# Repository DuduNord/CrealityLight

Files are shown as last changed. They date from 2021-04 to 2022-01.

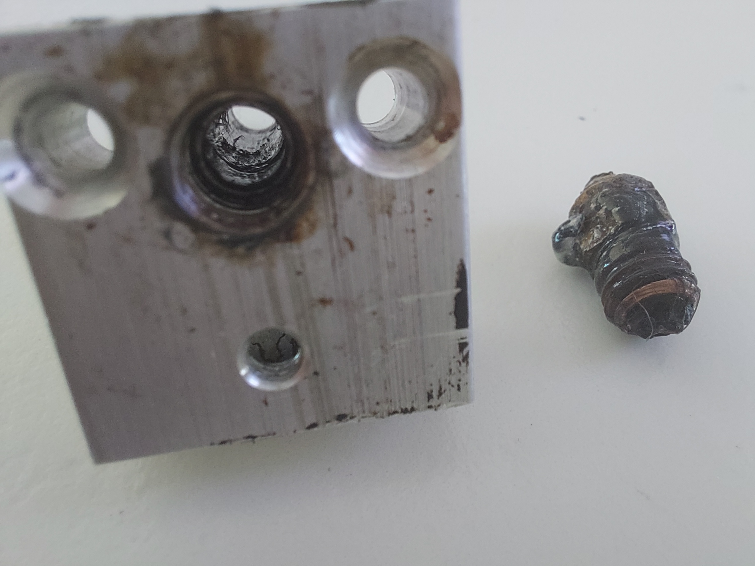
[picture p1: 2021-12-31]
For_Wiki/Issue1.jpg

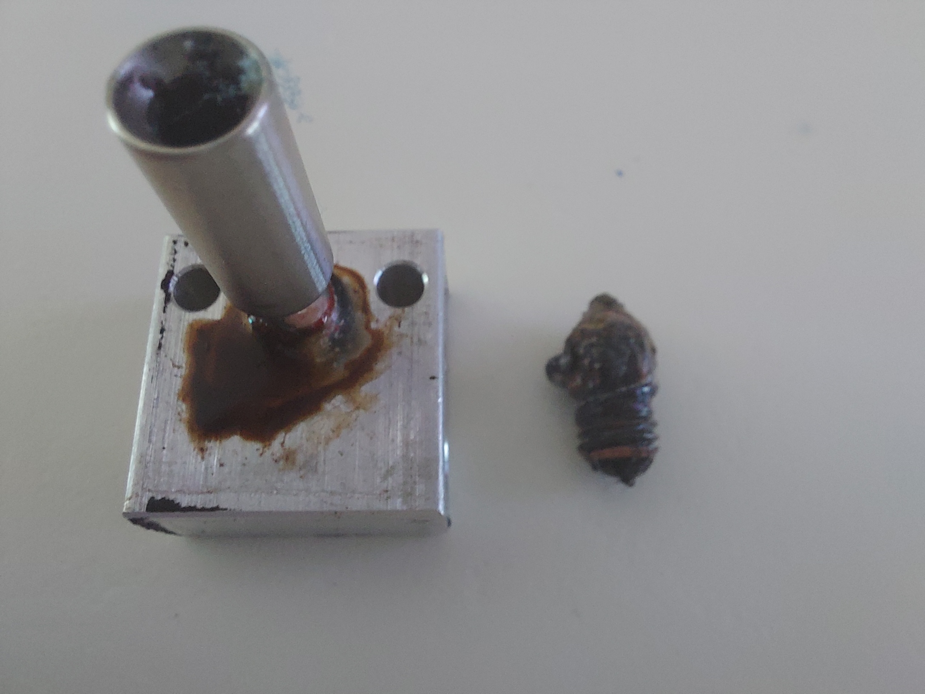
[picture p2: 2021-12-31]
For_Wiki/Issue2.jpg

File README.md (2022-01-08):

# CrealityLight V2 !!
## or how to connect a RPI/Ocroprint/Octoscreen and add some light 
### Read the wiki pages to get few more details.
This project does help how to connect a RPI to the octoscreen with a LED powerstage and a power relay.
This board does make the interface between the RPI and some MOS. 
But I have some doubt : 
- does the output of the relay goes to 0 when it is OFF ?
- how to turn on/off some LEDs manually without going to the octorpint interface, for a quick control ?
- how to turn off the RPI when the print is ended (the RPI can turn off the printer but may not turn it off) ?

I could have directly connected the RPI to the MOS, but I have decided to add an ATTINY1614 to add some flexibility.
I have added a puchbutton for some local interraction :
1. the pushbutton can turn on/off 3 different LED sting
1. it can also turn on/off a local LED (3V3) close to the extruder, to see the filament hole when we change it (this LED is not driven by the pi, only by the user because it is used to bring some light when I am changing the filament (I am not ont the onctoprint web interface)) 
1. it can force the RPI to be turned OFF locally :
   1. immediately (turn off the printer also)
   1. after a cooldown delay : the RPI is turned off immedately and the printer after some time (delay fixed in the ATTINY firmware)
   1. after a print, when the RPI does turn off the printer because of the idle time.
I also connect an emergency push button (direct connection) and plan to use a SmartFilamentSensor

## ATTINY connection

The Attiny does have to communicate with the PI. it has then to work under a 3.3V. The PRI does then provide a 3.3V to the ATTINY
The RPI is powered from the main printer AC/DC through a simple USB DC/DC. I have used a mEZS91202A from MPS (MonolithicPowerSystem) becaue of its simple connection. It can also deliver 2.5A : 
- https://www.monolithicpower.com/en/mezs91202a.html
- you can also consider a mEZD71202A-G for a 2A rail from 24V input (maybe it can also handle 3A)

The scheamtic and layout is in this project
The connection does use the end of the GPIO connector, to be able to use a touchscreen display for octodash/octoscreen : 
RPI GPIO | RPI BCM | ATTINY pin | ATTINY port | Signal description
-------- | ------- | ---------- | ----------- | ------------------ 
31 |  6|  4|  PA6| LED1IN
32 |  12|  3|  PA5| LED2IN
33 |  13|  2|  PA4| RelayIN : output of the PI to turn ON/OFF the relay
34 |  GND|  14|  GND| 
36 |  16|  5|  PA7| RPIReset : input for the PI, to be turned off
37 |  26|  na|  na| Emergency stop : push button to turn off a print if something goes wrong
38 |  20|  7|  PB2| OctoprintReady: signal from octoprint saying that it is alive
40 |  21|  na|  na| SmartSensor input : logic signal from a filament sensor

On the ATTINY board connector this mean :
ATTINY pin | ATTINY port | Arduino port | Signal description
---------- | ----------- | ------------ | ------------------
1 | 3.3V |  | power from a LDO on the board
2 | PA4 | 0 | RelayIN : signal from the PI
3 | PA5 | 1 | LED2IN : signal from the PI
4 | PA6 | 2 | LED1IN : signal from the PI
5 | PA7 | 3 | PI Reset : signal from the arduino to the PI to turn it off
6 | PB3 | 4 | PushButton : loacl button to select the action : turn ON/OFF the led or select which PI turn-off senario
7 | PB2 | 5 | OctoPrint Ready : signal from the PI saying that octoprint is ready (set to 1 when active)
8 | PB1 | 6 | LEDOUT : simple 3.3V LED, used for the Extruder
9 | PB0 | 7 | LEDPOWEROUT1 : MOS to 24V to drive one LED string
10 | UPDI | na | 
11 | PA1 | 8 | LEDPOWEROUT2 : MOS to 24V to drive one LED string
12 | PA2 | 9 | LEDPOWEROUT3 : MOS to 24V to drive one LED string
13 | PA3 | 10 | RELAYOUT : MOS to 24V to drive the printer relay
14 | GND |  | 

## Octoprint pluggins and config (see also the wiki)
quick note : the pluggin that turn off the RPI on a GPIO state has to be very carefully installed. I would recommend to disable the pin each time you disable it. otherwise, when you enable the pluggin in the octoprint "Pluggin Manager" it will immediately set the pin and activate it. And then your PI may turn off immediately becasue the pin is not driven

quick note : the pluggins can use GPIO or BCM numbering. Some give the choice like PSU Control. I would think that there is a mix when each pluggin does try to name the pins with different method. For the moment, the BCM method seems to be more functional.  

### Autoscroll (0.0.3)
### Bed Visualizer (1.0.0)
### BetterHeaterTimeout (1.3.0)
### Creality-2x-temperature-reporting-fix (0.0.4)
### DisplayLayerProgress Plugin (1.25.3)
### Emergency Stop Simplified (0.1.1) 

By default the pluggin does apply a pull-up or pull-down and check if the switch is open. If the button is set to GND, the pluggin does set a pull-up and will stop ONLY if the voltage is pulled-up by the internal pull-up resistor. By checking with an multimeter, I was no able to see a 3.3V on the pin when the switch is activated (open). I had a look then on the log (cd .octoprint/logs and then go really down to nano octoprint.log) and see the message : 
```
File "/home/pi/oprint/lib/python3.7/site-packages/octoprint_emergencystopsimplified/__init__.py", line 59, in _setup_button
    GPIO.setmode(GPIO.BCM)
ValueError: A different mode has already been set!
```
I tried then to change the mode from BCM to BOARD. I change the pin number to 37 (value in GPIO mode). A complete restart and I have been able to see that my pull-up was then present (I can see the voltage going up to 3,3V when the button is activated). During the print the printer goes immediately offline.

Note : Alexiri pluggin has the choice to turn off the printer or make a pause : https://github.com/alexiri/Emergency_stop_simplified/blob/master/octoprint_emergencystopsimplified/

Note : crysxd pluggin has the choice to select if the action is performed when the switch is going to open or closed state.
> would need to add an option to select BCM OR GPIO mode. And add a test mode like for the SmartFilament Sensor that has a specific "motion" test

My configuration: pin = 32 (GPIO pinout because I change from BCm to GPIO in the __init__.py) and button connected to ground.

### Exclude Region (0.3.0)
### Floating Navbar (0.3.4)
### Fullscreen Plugin (0.0.6)
### GPIO Shutdown (1.0.3)
- this pluggin would have worked perfectly but it seems to mix at start-up the BCM and GPIO pins. to get it funcional, I have to select in the setup the GPIO number that I want (and not the BCM one) and save. Then the LED is turned ON immediately. Consider to use instead a simple script/service that is available on the web and out of octoprint. I wil otherwise change the Jinja config file to link the BCM pin to the GPIO.
- the pluggin location is in "~/oprint/lib/python2.7/site-packages/octoprint_GPIOShutdown"
- to get it functional, I have changed manually the JINJA2 file to allow the selection of pins up to 40. By doing this, I can select a high pin number.
- My setup : shutdown on pin GPIO36 / PIN LED : GPIO 38 with default debounce time.
- To get this, i have to change the jinja file the selection menu for both the led and the shutdown pin:
```
cd ~/oprint/lib/python2.7/site-packages/octoprint_GPIOShutdown/templates/
nano GPIOShutdown_settings.jinja2
                                <option value="-1">Disabled</option>
                                <option value="2">BCM 2</option>
                                <option value="3">BCM 3</option>
                                <option value="4">BCM 4</option>
                                <option value="5">BCM 5</option>
                                <option value="6">BCM 6</option>
                                <option value="7">BCM 7</option>
                                <option value="8">BCM 8</option>
                                <option value="9">BCM 9</option>
                                <option value="10">BCM 10</option>
                                <option value="11">BCM 11</option>
                                <option value="12">BCM 12</option>
                                <option value="13">BCM 13</option>
                                <option value="14">BCM 14</option>
                                <option value="15">BCM 15</option>
                                <option value="16">BCM 16</option>
                                <option value="17">BCM 17</option>
                                <option value="18">BCM 18</option>
                                <option value="19">BCM 19</option>
                                <option value="20">BCM 20</option>
                                <option value="21">BCM 21</option>
                                <option value="22">BCM 22</option>
                                <option value="23">BCM 23</option>
                                <option value="24">BCM 24</option>
                                <option value="25">BCM 25</option>
                                <option value="26">BCM 26</option>
                                <option value="27">BCM 27</option>
                                <option value="3">GPIO 3</option>
                                <option value="5">GPIO 5</option>
                                <option value="7">GPIO 7</option>
                                <option value="8">GPIO 8</option>
                                <option value="10">GPIO 10</option>
                                <option value="11">GPIO 11</option>
                                <option value="12">GPIO 12</option>
                                <option value="13">GPIO 13</option>
                                <option value="15">GPIO 15</option>
                                <option value="16">GPIO 16</option>
                                <option value="18">GPIO 18</option>
                                <option value="19">GPIO 19</option>
                                <option value="21">GPIO 21</option>
                                <option value="22">GPIO 22</option>
                                <option value="23">GPIO 23</option>
                                <option value="24">GPIO 24</option>
                                <option value="26">GPIO 26</option>
                                <option value="29">GPIO 29</option>
                                <option value="31">GPIO 31</option>
                                <option value="32">GPIO 32</option>
                                <option value="33">GPIO 33</option>
                                <option value="35">GPIO 35</option>
                                <option value="36">GPIO 36</option>
                                <option value="37">GPIO 37</option>
                                <option value="38">GPIO 38</option>
                                <option value="40">GPIO 40</option>
```
Backup : a local service routine:  
Let's try with this config (https://www.instructables.com/Simple-Raspberry-Pi-Shutdown-Button/) to get a shutdown on level 1 because the ATTINY when OFF (not powered-up) will pull the pin low :
gpio_pin_number=21
GPIO.setmode(GPIO.BCM)
GPIO.setup(gpio_pin_number, GPIO.IN, pull_up_down=GPIO.PUD_DOWN)
try:
    GPIO.wait_for_edge(gpio_pin_number, GPIO.RISING)
    os.system("sudo shutdown -h now")
except:
    pass
GPIO.cleanup()

### LED Strip Control (0.3.7) (not installed)
### LightsOut (0.1.2)
### Multi Colors (1.0.17) 
### OctoLight (0.1.1)
> Configuration : Light pin = 38
### PSU Control (0.1.11)
to be changed, checked : For some reason, the pluggin does not work if the pin mode is GPIO. But it does work well when the BCM mode is selected. you need to change again th python to select the "BOARD" mode instead of "BCM"
> Configuration : GPIO mode : Board > GPIO pin > 37 // internal sensing (5s)
### Simple Emergency Stop (1.0.4) 
### Smart Filament Sensor (1.1.5.3)
Board mode / pin 40 with the button "enable sensor" checked > command M600 (to be tested), detection mode : distance set at 15mm (default value)
and then tested with the small test button
### Tab Order (0.5.12) 
### not acivated - Octoprint-Display-ETA (1.1.3) 
### WebcamTab (0.2.0)

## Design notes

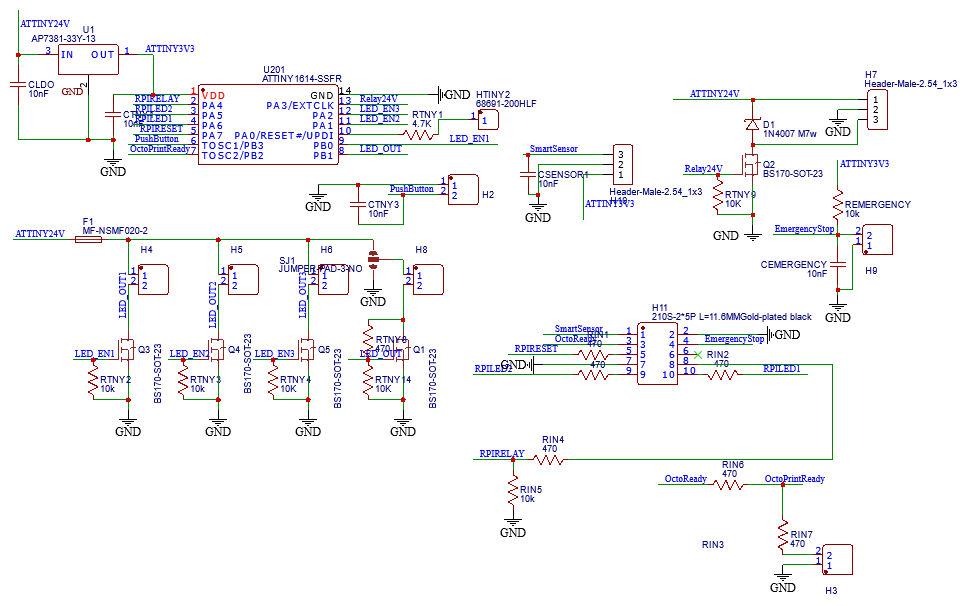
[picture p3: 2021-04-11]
Schematic_CrealityLight_2021-04-11.png

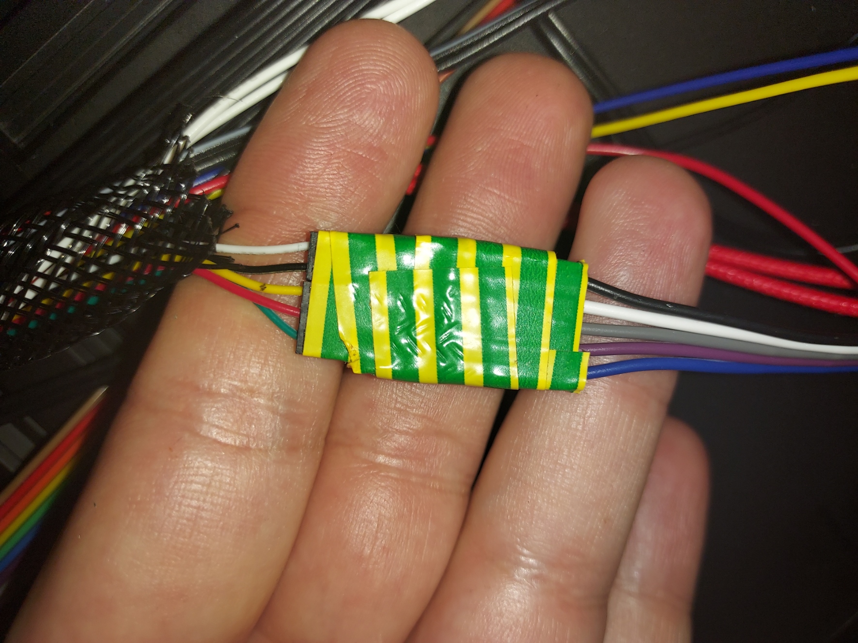
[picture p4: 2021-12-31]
For_Wiki/BLTOUCH_picture2.jpg

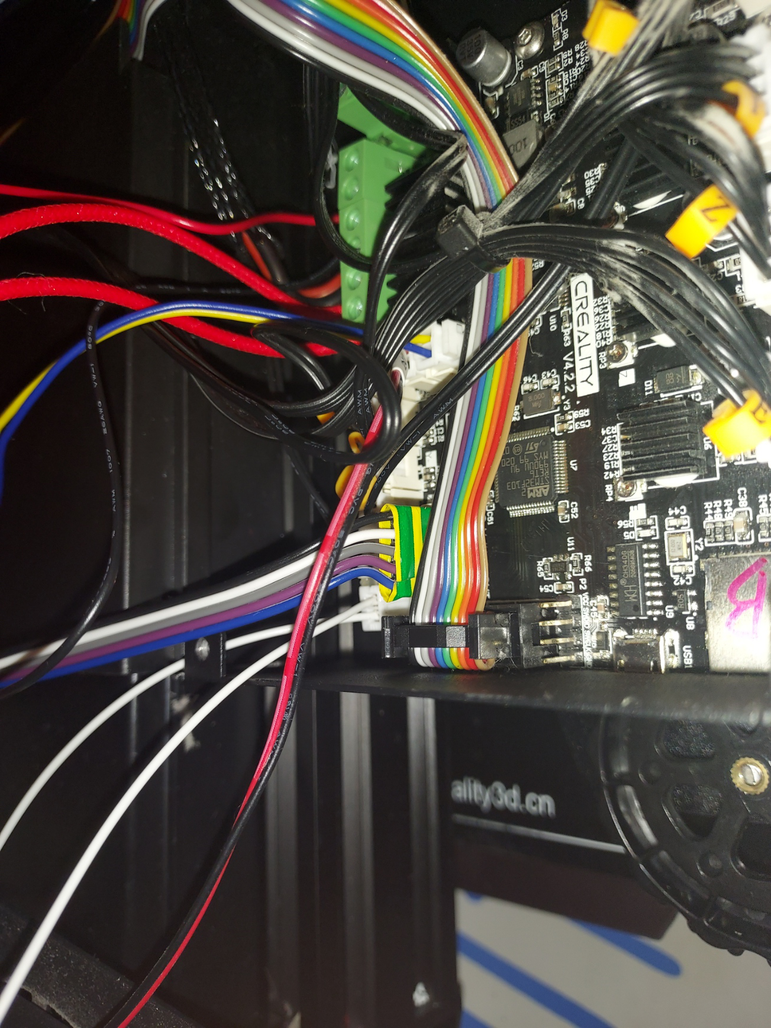
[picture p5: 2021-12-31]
For_Wiki/BLTOUCH_picture1.jpg

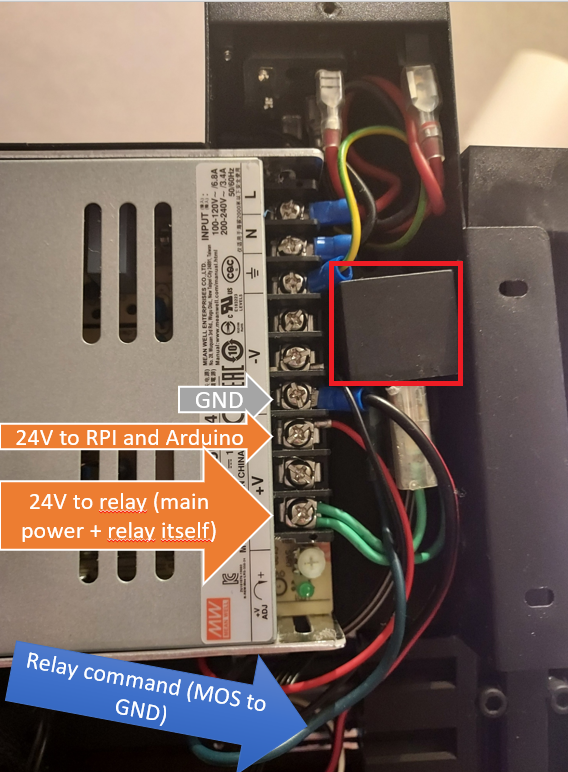
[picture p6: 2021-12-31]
For_Wiki/RelayCreality.png

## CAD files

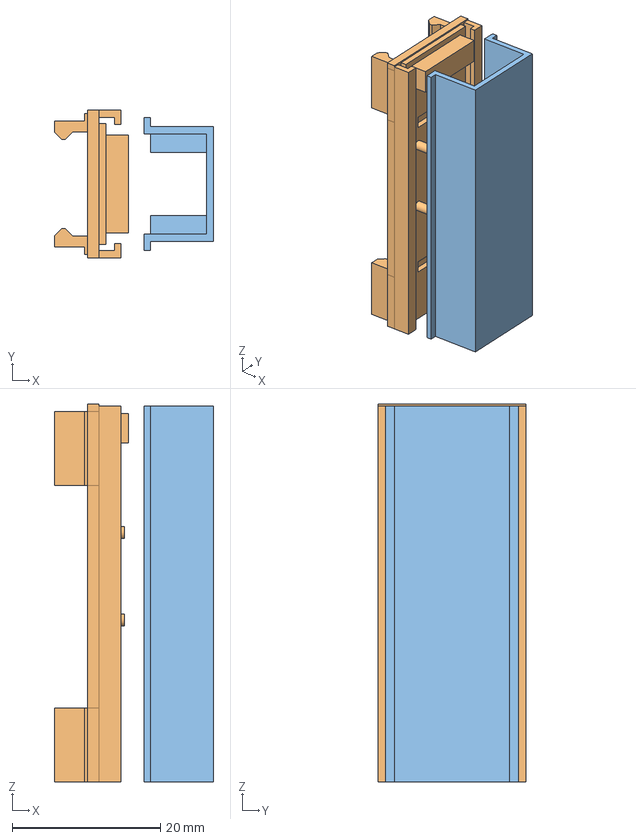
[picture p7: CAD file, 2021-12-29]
RailEnder3USB-V2.FCStd
21.5 x 20.0 x 51.0 mm
SupportUsbBase
SupportUsbAClipper
Capot

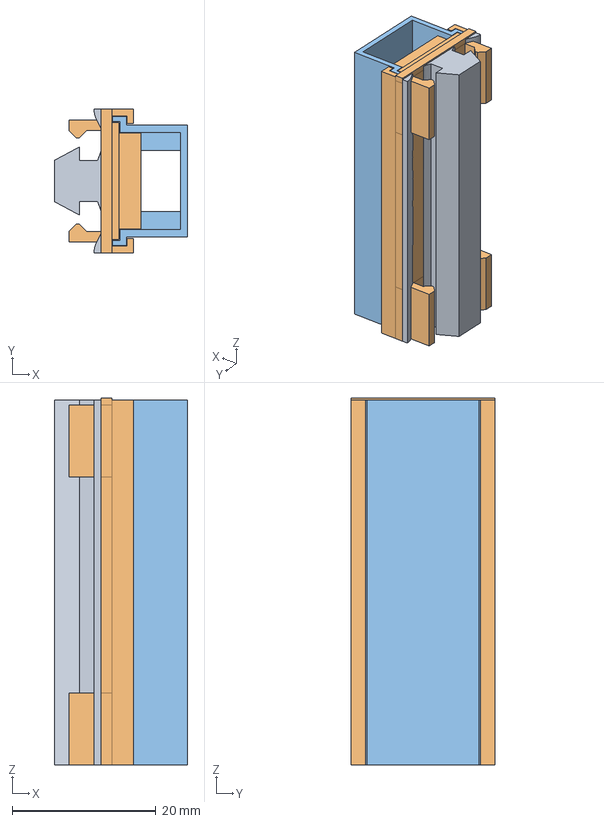
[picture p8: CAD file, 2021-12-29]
RailEnder3USB.FCStd
18.5 x 20.0 x 51.0 mm
RailAGlisser
SupportUsbAClipper
Capot

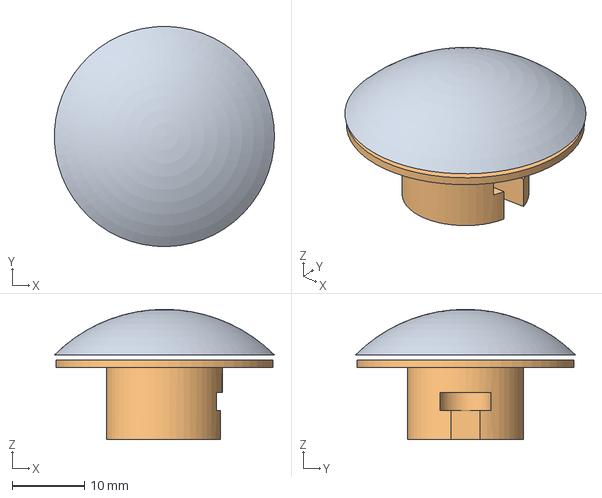
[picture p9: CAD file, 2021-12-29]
EmmergencyChampi.FCStd
30.4 x 30.4 x 18.0 mm
Champignon

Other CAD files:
RailEnder3USB-V2.stl

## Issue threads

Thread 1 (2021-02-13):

Printer turned on at startup

DuduNord, 2021-02-13:

DuduNord, 2021-02-13:
Am implementing a sensing methid that wait for the RPI to turn off the relay before going into the main program

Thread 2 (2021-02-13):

When the RPI is not present or not functional/booting, no printer available

DuduNord, 2021-02-13:
If the RPI can't work, for any reason, the printer can't be turned on. this could be manage by pull-up/down resistor if the PI is not present. But to be sure, and to avoid any effect on ISSUE1 (does wait a modification of relay command to turn on), will implement a sensing method with the button : if the button is activated at power on, the relay is always on immediately> the RPI will not be able to turn on/off the printer. anyway  the LEDs will stay active from the RPI or the push button

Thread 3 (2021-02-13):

At power down, printer restart

DuduNord, 2021-02-13:
When the end user does urn off the RPI through the ATTINY, (4 click/5 click or long press), the ATTINY does know that the RPI is turned off (becasue it does it itself). Then the Relay and lights are also turned off. but when the end-user turn off the printer and the RPI remotely (push-button not activated), the ATTINY will turn on again the printer and the light again (same root cause than issue 1). Unfortunately there is no way for the  ATTINY to know that Octoprint is used.
To fix this, we will use PSUControl pluggin to indicate (by a signal, was planned to be a LED) that octoprint is up and running. ATTINY will have only one LED signal and we will use the second LED signal (not used in my case for the moment) to get this signal and "sense" octoprint activity.
At boot it will not trust the pin but will get its variable "RPI eteint" (=RPI turned off) to "true" to know that it is turned off.

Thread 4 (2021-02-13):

When use OctoRemote, I can't start the printer because PowerOn button from PSU Control pluggin not present

DuduNord, 2021-02-13:
If I want to launch a print from the smartphone, I can't turn on the printer because the app does not show the on/off button from the pluggin. I need then to go through the internet interface to turn on the printer.

DuduNord, 2021-02-13:
To overcome this, will implement a funciton in the boot : if the button is activated when the power is applied, the printer will be turned on, whatever the PI status (if present or not, if booting or functional). Later if the RPI is connected, it will be possible to "recover" the ON/OFF function from the PI, by turning on the button on the web page.

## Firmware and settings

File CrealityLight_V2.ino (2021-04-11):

/* V3: utilisation d'une entrée GPIOSHUTDOWN

 * FONCTIONNEMENT LED : 
 * si le pi n'a pas activé la lumière LED2  alors l'utilisateur peut allumer éteindre avec respectivement un appui simple et un double appui
 * si le pi n'a pas activé la lumière LED1, un appui long allume LED1 et le relachement l'éteint
 * si l'utilisateur appui 3 fois, éteint/allume la LED de l'extrudeur * Fonctionnement Relais/extinction
 * la sortie LED3 n'est pas utilisé
 * FONCTIONNEMENT EXTINCTION
 * si l'utilisateur appui 4 fois, l'Arduino éteindra le PI lorsque le PI éteindra l'imprimante (mode suicide). Autre 4 click = annule l'extinction
 *   si l'utilisateur a validé l'extinction du PI par le bouton, alors éteindra le PI en activant la pin "RPIReset" après un certain délais (idéalement passage de 0 à 1 pui de 1 à 0)
 *   Mais l'utilisateur peu désactiver cette extinction avec la même séquence (4 appui)
 * si l'utilisateur appui 5 fois, l'Arduino éteind le PI immédiatement et éteindra l'imprimante après un délais pour la laisser refroidir. Pas d'annulation possible
 * Si l'utilisateur fait un appui long sur le bouton, alors l'Arduino éteint tout immédiatement (imprimante et PI)
 * NOTE : a la sélection de 4 ou 5 appuis, la LED de l'extruder clignotera du meme nombre de click, pour valider la prise en compte
 * A FAIRE : 
 *    Alimentation de l'imprimante au démarrage si on appuie sur le bouton au démarage
 */

/*        PINOUT
 *        ------
 *          VDD  |      |GND
 *RelayIN/0/PA4  |      |PA3/10 /RelayOut
 *LED2IN /1/PA5  |      |PA2/9  /LedPowerOut3
 *LED1IN /2/PA6  |      |PA1/8  /LedPowerOut2
 *RPIRst /3/PA7  |      |PA0/11 /ISP
 *PushBut/4/PB3  |      |PB0/7  /LedPowerOut1
 *OctoRdy/5/PB2  |      |PB1/6  /LedOut
 *        ------*/

/* SOIC  Pin   Arduino  ADC0  ADC1  DAC0  USART0  SPI0  TWI0  TCA0  TCBn    TCD0  CCL   
 * 10    PA0   11       AIN0  -     -     -       -     -     -     -       -     LUT0-IN0  > ISP
 * 11    PA1   8        AIN1  -     -     TXDbis  MOSI  SDA   -     -       -     LUT0-IN1  > LedPowerOut2
 * 12    PA2   9        AIN2  -     -     RXDbis  MISO  SCL   -     -       -     LUT0-IN2  > LedPowerOut3
 * 13    PA3   10       AIN3  -     -     XCKbis  SCK   -     WO3   TCB1 WO -     -         > RelayOut
 * 14    GND            -     -     -     -       -     -     -     -       -     -         >
 * 1     VDD            -     -     -     -       -     -     -     -       -     -         >
 * 2     PA4   0        AIN4  AIN0  -     XDIRbis SS          WO4           WOA   LUT0-OUT  > RelayIN > RPI PIN 33
 * 3     PA5   1        AIN5  AIN1  -     -       -     -     WO5   TCB0 WO WOB             > LED2IN > RPI PIN 32
 * 4     PA6   2        AIN6  AIN2  OUT                                                     > LED1IN > RPI PIN 31
 * 5     PA7   3        AIN7  AIN3  -     -       -     -     -     -       -     LUT1-OUT  > RPIReset
 * 6     PB3   4        -     -     -     RXD     -     -     WO0bis                        > PshBut
 * 7     PB2   5        -     -     -     TXD     -     -     WO2                           > OctoReady > > RPI PIN 38 (BCM GPIO20)
 * 8     PB1   6        AIN10 -     -     XCK     -     SDA   WO1                           > LedOut
 * 9     PB0   7        AIN11 -     -     XDIR    -     SCL   WO0                           > LedPowerOut1
 */

#include "EButton.h"
#define DEBUGMODE         // le laisser car le reste est pas testé (prise en main )

/* ---------------------------------------------------------- */
/* ------------------  HARDWARE  ---------------------------- */
/* ---------------------------------------------------------- */
/* Ajouter ATTINY1614 dans Arduino : 
 *  https://create.arduino.cc/projecthub/john-bradnam/using-the-new-attiny-processors-with-arduino-ide-612185
 * Arduino : MegaTinyCore>>ATTINY1614....
 * Bootloader : jtag2updi (megaTinyCore) à base d'un Arduino Nano Old bootloader
 * Info > BOD Volt:2,6V // Clock 1MHz // Mili by default // UART close to 3V
 * please reade this great tutorial to know what you can do with ATTINY MegaTinyCore : https://github.com/SpenceKonde/megaTinyCore 
*/
/* ---------------------------------------------------------- *
 * -------------------  PINOUT  ----------------------------- *
 * ---------------------------------------------------------- */
#define LedPowerOut1        7  //PB0 > SORTIE transistor LED
#define LedPowerOut2        8  //PA1 > SORTIE transistor LED
#define LedPowerOut3        9  //PA2 > SORTIE transistor LED
#define LedOut              6  //PB1 > SORTIE simple LED pour extrudeur
#define RelayOut            10 //PA3 > SORTIE relais 24V/16A
#define RPIReset            3  //PA7 > SORTIE : sortie à la 0 pour éteinde le pi
#define PshBut              4  //PB3 > ENTREE SEULE bonton poussoir en pull-up de commande pour interface homme Arduino
#define LED1IN              2  //PA6 > ENTREE VENANT DU PI
#define LED2IN              1  //PA5 > ENTREE VENANT DU PI
#define RelayIN             0  //PA4 > ENTREE VENANT DU PI
#define GPIOSHUTDOWNIN      5  //PB2 > ENTREE VENANT DU PI INDIQUANT SI OCTOPRINT EST PRET OU PAS

EButton button(PshBut);     //bouton pressé quand à la masse

/* ---------------------------------------------------------- */
/* -----------------  CONSTANTES  --------------------------- */
/* ---------------------------------------------------------- */
// pour séquence d'initialisation
#define DelaisStartup                         60000    // délais avant que l'ATTINY commence sa boucle principale et allume le relais et les lumières. nécessaire car pendant le boot, le PI allume le relais temporairement

// variables 
#define DureePression                         984    // en milli secondes
#define DureePressionLongue                   3000   // en milli secondes
#define DelaisExtinctionPiParPi               1000   // délais (ms) entre le moment ou l'imprimante est éteinte par le PI et le moment ou le PI est éteint par l'Arduino
#define DelaisExtinctionPiRefroidissement    120000  // délais (ms) entre le moment ou l'Arduino détecte une extinction et le moment ou il éteint l'imprimante (délais nécessaire pour refroidir le bed et l'extrudeur)
#define DelaisExtinctionPiImmediat            1000   // délais (ms) entre le moment ou l'imprimante est éteinte et le moment ou le PI est éteint (extinction immédiate)
#define DelaisReboot                          60000   // délais (ms) entre le moment ou l'imprimante est éteinte et le moment ou le PI est éteint (extinction immédiate)
#define DeglitchRelaisIn                      400    // délais (ms) pendant lequel l'entrée venant du pi doit rester à 0 avant l'extinction réelle du relais de l'imprimante

#define LED1PWM                      255          // valeur de PWM entre 0 et 255
#define LED2PWM                      255
#define LED3PWM                      255          // pas implémenté pour le moment
#define LED4PWM                      255          // sortie extrudeur

#define PIRESETE                      1           // Etat a applique pour éteindre le PI
#define PIFONCTIONNE                  0           // Etat a applique pour laisser le PI fonctionner

// constantes pour mieux lire l'état de GPIOSHUTDOWNSequenceVerif
#define STARTUP                       0
#define WAITTOBOOT                    1
#define BOOTED                        2
#define POTENTIALREBOOTED             3
#define TURNEDOFF                     4

/* pour changer la vitesse de clock, pas utilisé
#define MCLK_PRESC_2    0x00
#define MCLK_PRESC_4    0x01
#define MCLK_PRESC_8    0x02
#define MCLK_PRESC_16   0x03
#define MCLK_PRESC_32   0x04
#define MCLK_PRESC_64   0x05
#define MCLK_PRESC_6    0x08h
#define MCLK_PRESC_10   0x09
#define MCLK_PRESC_12   0x0A
#define MCLK_PRESC_24   0x0B
#define MCLK_PRESC_48   0x0C */

/* ---------------------------------------------------------- */
/* -----------------  VARIABLES  ---------------------------- */
/* ---------------------------------------------------------- */
bool ExtinctionPiParPi = false;      // TRUE, si l'utilisateur a demandé à éteindre le PI en même temps que l'imprimante, 
bool ExtinctionPiRefroidissement = false;      // TRUE, si l'utilisateur a demandé à éteindre le PI après un délais de refroidissement, 
bool ExtinctionPiImmediat = false;      // TRUE, si l'utilisateur a demandé à éteindre le PI immédiatement 
bool EntreePiRelais = false;            //variables pour le deglich de l'entrée relais venant du PI
bool EntreePiRelaisPrev = false;
bool EtatRelais = false;                // donne l'état du relais

uint8_t EtatRelaisBoot = 0;                // donne l'état du relais au boot du PI
uint8_t EtatGPIOSHUTDOWNIn = 0;            // donne l'état de la pin de status "GPIOShutdown" au boot, pour voir si elle bagotte ou reste à 0
uint8_t GPIOSHUTDOWNSequenceVerif = STARTUP;     // donne l'état du relais au boot du PI
bool EtatBoutonBoot = false;                // donne l'état du bouton poussoir au boot
uint8_t EtatBoutonBootPrev = 0;             // donne l'état du relais au boot du PI, UINT pour le comparer directement à la lecture de l'entrée qui renvoie un entier 0 ou 1 (pourrait fonctionner avec un bool mais bon....)
bool BoutonNotActivated = true;             // indique si le bouton a été activé ou non pendant le boot
bool BootTimerEnded = false;                // indique si le timer de boot s'est terminé sans changement d'état de pin du PI

bool EntreePiLED1 = false;            //variables pour le deglich de l'entrée LED1 venant du PI
bool EntreePiLED1Prev = false;
bool EntreePiLED2 = false;            //variables pour le deglich de l'entrée LED2 venant du PI
bool EntreePiLED2Prev = false;

bool PiEteint = false;          // TRUE, si le pi a été éteint par l'Arduino 
unsigned long TimeExtinctionPiParPi=0;
unsigned long TimeExtinctionPiRefroidissement=0;
unsigned long TimeExtinctionPiImmediat=0;
unsigned long TimePotentialReboot=0;

unsigned long TimeDeglichRelais=0;
unsigned long TimeRelaisOff=0;

uint8_t PrevLED1IN = 0;
uint8_t PrevLED2IN = 0;
bool EtatClick1   = false;
bool EtatClick2   = false;

bool SimpleLed = false;   // la LED 3.3V de l'extrudeur

/* ---------------------------------------------------------- */
/* --------------  FONCTIONS BOUTON  ------------------------ */
/* ---------------------------------------------------------- */
// btn.getClicks() pour avoir le nombre de click 
// isButtonPressed() - Test if the button was pressed the last time it was sampled.
// isLongPressed() - Test it the button is in long-pressed state.
// getStartTime() - Returns the time of the first button press.
// getPrevTransitionTime() - Time of a previous transition. Returns startTime for the first transition.


void transitionHandler(EButton &btn) {      //triggered each time the button state changes from pressed to released, or back
}
void eachClickHandler(EButton &btn) {       //triggered each time the key  is released, unless it was in LONG_PRESSED state;
}
void singleClickHandler(EButton &btn) {     //triggered when there was exactly one click;
}
void doubleClickHandler(EButton &btn) {     //triggered when there were exactly two clicks;
}

void doneClickingHandler(EButton &btn) {    //triggered after all the clicks have been counted (use getClicks() to get the clicks count);
/* difference between EACH_CLICK and DONE_CLICKING: 
 * the first one is called each time the key is released (unless it was a long-press), 
 * while DONE_CLICKING is called once, at the end of clicks counting.
 */ 
	// on devrait tester ici si le bouton est un appui long ou pas. car à l'extinction immédiate du PI, cala risque d'être vu comme un seul click et générer un petit flash sur LED1 
  
  switch (btn.getClicks()) {
/* pour les 2 lumières commandées par le PI, on va considérer qu'il n'y a pas de PWM
 * Si le pi a sa commande à 0, le bouton peut allumer et éteindre la lumière
 * si le pi a sa commande à 1, le bouton complémente la sortie tant que la pin ne redescend pas à 0*/    
    case 1:
      if (EtatClick1) {
        EtatClick1 = false;
        digitalWrite(LedPowerOut1,0);
      } else {
        EtatClick1 = true;
        analogWrite(LedPowerOut1,LED1PWM);
      }
      break;

    case 2:
      if (EtatClick2) {
        EtatClick2 = false;
        digitalWrite(LedPowerOut2,0);
      } else {
        EtatClick2 = true;
        analogWrite(LedPowerOut2,LED2PWM);
      }
      break;

    case 3:
      if(SimpleLed) {
        SimpleLed = false;
        digitalWrite(LedOut,0);
      } else {
        SimpleLed = true;
        analogWrite(LedOut,LED4PWM);
      }
      break;

    case 4:
      if(ExtinctionPiParPi) {
        ExtinctionPiParPi = false;
        ExtinctionPiRefroidissement = false;
        ExtinctionPiImmediat = false;
        TimeExtinctionPiParPi = 0;
      } else {
        ExtinctionPiParPi = true;
        ExtinctionPiRefroidissement = false;
        ExtinctionPiImmediat = false;
        TimeExtinctionPiParPi = millis();
      }
      ValidationExtrudeur(4);
      break;

    case 5:
      if(ExtinctionPiRefroidissement) {
        ExtinctionPiParPi = false;
        ExtinctionPiRefroidissement = false;
        ExtinctionPiImmediat = false;
        TimeExtinctionPiRefroidissement = 0;
      } else {
        ExtinctionPiParPi = false;
        ExtinctionPiRefroidissement = true;

        ExtinctionPiImmediat = false;
        TimeExtinctionPiRefroidissement = millis();
      }
      ValidationExtrudeur(5);
      break;

    default:
      break;
  }
}
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
void loop() {
  if(BoutonNotActivated == false)
    button.tick();    // fonction qui vérifie le bouton

/* gestion des LEDs
 * si le pi demande à allumer alors que la sortie est déja allumée, alors ne fait rien, ou sinon l'allume
 * Si le pi demande à éteindre alors que la sortie est allumée, alors éteint */
  if(PiEteint == false) {               // sinon, si le PI est éteint alors on peut toujours allumer les LEDs par le bouton
    if(digitalRead(LED1IN) == 1) {
      if(!PrevLED1IN) {
          // changement d'état
          EtatClick1 = true;
          analogWrite(LedPowerOut1,LED1PWM);
        }
        PrevLED1IN = true;
    } else {
        if(PrevLED1IN) {
          // changement d'état
          EtatClick1 = false;
          digitalWrite(LedPowerOut1,0);
        }
        PrevLED1IN = false;
    }
    if(digitalRead(LED2IN) == 1) {
        if(!PrevLED2IN) {
          // changement d'état
          EtatClick2 = true;
          analogWrite(LedPowerOut2,LED2PWM);
        }
        PrevLED2IN = true;
    } else {
        if(PrevLED2IN) {
          // changement d'état
          EtatClick2 = false;
          digitalWrite(LedPowerOut2,0);
        }
        PrevLED2IN = false;
    }
  }

//gestion de l'extinction
/* si le bouton est validé par 4 clic, le pi sera éteint quand le relais sera éteint + DelaisSuicide. il faut attendre que le relais s'éteigne
 * si le bouton est validé par 5 clic, extinction immédiate après DelaisImprimanteSuiteSuicide 
 * si l'utilisateur veut éteindre tout de suite, un appui long */

  if(ExtinctionPiImmediat && (millis() - TimeExtinctionPiImmediat > DelaisExtinctionPiImmediat)) {      // extinction immédiate par appuis long
    SequenceResetPi();
    digitalWrite(RelayOut,0);
    EtatRelais = false;
    ExtinctionPiImmediat = false;
  } else {
    if(ExtinctionPiRefroidissement) {   // on éteint le pi d'abors et on attend un délais avant d'éteindre l'imprimante
      if(PiEteint == false) {
        SequenceResetPi();              // extinction du PI et des LEDs
      }
      if(millis() - TimeExtinctionPiRefroidissement > DelaisExtinctionPiRefroidissement) {
        digitalWrite(RelayOut,0);
        EtatRelais = false;
        ExtinctionPiRefroidissement = false;
      }
    } else {            // 
      if(PiEteint) {    // par défaut à false
        digitalWrite(RelayOut,0);
        EtatRelais = false;
      } else {          // si le PI est allumé, on va tester le mode suicide

        // prise en compte de l'entrée GPIO Shutdown > si le PI est éteint par le réseau, alors la pin tombe et l'Arduino peut éteindre l'imprimante (pas les lumières). On simule le bouto appuyé 4fois
        // on doit attendre que le PI ait booté car sinon, l'arduino va l'éteindre de suite. On fait donc uin pooling de la pin pour changer l'état de GPIOSHUTDOWNSequenceVerif 
        switch (GPIOSHUTDOWNSequenceVerif) {
          case STARTUP:     
            GPIOSHUTDOWNSequenceVerif = WAITTOBOOT;
            break;

          case WAITTOBOOT:
            if (digitalRead(GPIOSHUTDOWNIN) == 1) {
              delay(500);
              if (digitalRead(GPIOSHUTDOWNIN) == 1) {      // délais de 500m pour deglich, on reteste la pin pour savoir si elle est bien à 1, si le pi est bien démarré
                GPIOSHUTDOWNSequenceVerif = BOOTED;
              }
            }
            break;

          case BOOTED:
            if (digitalRead(GPIOSHUTDOWNIN) == 0) {
              delay(500);
              if (digitalRead(GPIOSHUTDOWNIN) == 0) {      // délais de 500m pour deglich, on reteste la pin pour savoir si elle est bien à 0, si le pi est bien off
                GPIOSHUTDOWNSequenceVerif = POTENTIALREBOOTED;
                TimePotentialReboot = millis();
              }
            }
            break;

          case POTENTIALREBOOTED:       // on attend une tempo avant de considérer octoprint réellement éteint
            if (millis() - TimePotentialReboot > DelaisReboot) {
              GPIOSHUTDOWNSequenceVerif = TURNEDOFF;
            } else {
              if (digitalRead(GPIOSHUTDOWNIN) == 1) {
                delay(500);
                if (digitalRead(GPIOSHUTDOWNIN) == 1) {      // délais de 500m pour deglich, on reteste la pin pour savoir si elle est bien à 1, si le pi est bien démarré
                  GPIOSHUTDOWNSequenceVerif = BOOTED;
                }
              }
            } 
          break;

          case TURNEDOFF:            //si octoprint est arrêté, on peut éteindre le pi
            ExtinctionPiParPi = true;                 // pour éteindre plus bas
            ExtinctionPiRefroidissement = false;
            ExtinctionPiImmediat = false;
            TimeExtinctionPiParPi = millis();
            TimeRelaisOff = millis();
            digitalWrite(RelayOut,0);
            EtatRelais = false;
            break;

          default:
            break;

        }  

 #ifdef DEBUGMODE                                 // mode DEBUG : gestion simple du relais, on recopie la pin du RPI
        if (digitalRead(RelayIN) == 1) {          // si allumage (état haut), on le fait immédiatement
          digitalWrite(RelayOut,1); 
          EtatRelais = true;
          EntreePiRelais = true;
          EntreePiRelaisPrev = true;
          TimeDeglichRelais = 0;
        } else {                            // si extinction, deglich de "DeglitchRelaisIn" ms (si le pi n'est pas présent, la pull-up interne va mettre la pin à '1')
          EntreePiRelais = false;
          if(EntreePiRelaisPrev != EntreePiRelais) {    // on est à la détection du front
            TimeDeglichRelais = millis();
          } else {                                      // on est à la détection du front
            if(millis() - TimeDeglichRelais > DeglitchRelaisIn) {
              if(EtatRelais)
                TimeRelaisOff = millis();         // on sauvegarde le temps de mise à 0 une seule fois, avant que l'état du relais ne soit changé. comme ca à la prochaine boucle ce timing ne sera pas continuellement modifié à l'heure courante
              digitalWrite(RelayOut,0);
              EtatRelais = false;
            }
          }
          EntreePiRelaisPrev = EntreePiRelais;
        }
 #else                                            // autre que mode DEBUG > il faut tenir compte de l'allumage sans pi puis le boot de ce dernier qui pourra reprendre la main
        // prise en compte du flag "EtatBoutonBoot" 
        // si le bouton n'a pas été activé au boot, le PI commande le relais normalement
        if((!EtatBoutonBoot) && (GPIOSHUTDOWNSequenceVerif != 2)) {       // si GPIOSHUTDOWNSequenceVerif = 2, ca veut dire que le RPI doit s'éteindre ou est déjà éteint
          if (digitalRead(RelayIN) == 1) {          // si allumage (état haut), on le fait immédiatement
            digitalWrite(RelayOut,1); 
            EtatRelais = true;
            EntreePiRelais = true;
            EntreePiRelaisPrev = true;
            TimeDeglichRelais = 0;
          } else {                            // si extinction, deglich de "DeglitchRelaisIn" ms (si le pi n'est pas présent, la pull-up interne va mettre la pin à '1')
            EntreePiRelais = false;
            if(EntreePiRelaisPrev != EntreePiRelais) {    // on est à la détection du front
              TimeDeglichRelais = millis();
            } else {                                      // on est à la détection du front
              if(millis() - TimeDeglichRelais > DeglitchRelaisIn) {
                if(EtatRelais)
                  TimeRelaisOff = millis();         // on sauvegarde le temps de mise à 0 une seule fois, avant que l'état du relais ne soit changé. comme ca à la prochaine boucle ce timing ne sera pas continuellement modifié à l'heure courante
                digitalWrite(RelayOut,0);
                EtatRelais = false;
              }
            }
            EntreePiRelaisPrev = EntreePiRelais;
          }
        } else {      // si le bouton a été activé au démarrage, le relais est en marche mais le PI a sa sortie désactivé (à 1). Si le PI a fini de booter dans les temps, il suffit que le PI veuille allumer le relais pour reprendre la main
                    // il est important que cette séquence n'arrête pas une impression en court
          if((BootTimerEnded == false) && (digitalRead(RelayIN) == 1))    // si le pi a bien booté dans les temsp et qu'il active sa sortie relais
            EtatBoutonBoot = false;         // le pi reprend la main
        }
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

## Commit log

2021-12-29 Add files via upload
    These are the 2 Freecad files that I made for an emergency stop button and a case for "mEZS91202A" board from MPS that generate the 5V for the PI from the 24V main power supply
    [EmmergencyChampi.FCStd, RailEnder3USB.FCStd]
2021-12-29 Add files via upload
    Easier support for mEZS91202A as the cover is easier to insert in the main base. Also added the STL with the 2 parts. You can use MASH tool to split them in 2 and print them in ~ 1h+40mn with low qua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
    [RailEnder3USB-V2.FCStd, RailEnder3USB-V2.stl]
